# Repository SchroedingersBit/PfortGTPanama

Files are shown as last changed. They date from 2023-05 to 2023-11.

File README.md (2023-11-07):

# PfortGT World Final Panama 2023 🤖

## Introduction
This is the GitHub repository for the autonomous driving car of the **PfortGT Team** of the **Landesschule Pforta from Germany** for the **WRO Future Engineers World Final 2023 in Panama**.
In this repository we go into our planning - and building process for our car. We describe our problems and ideas we had along the way and explain our construction plans and programs.
## Overview
Our car is powered by an Arduino. It consists of a chassis which is equipped with individually 3D-printed mounts for the various sensors and the camera (see [components](/vehicle/components)). Power is supplied by a rechargeable battery (see [electronics](/vehicle/electronics)). The sensor equipment consists of three ultrasonic sensors, a gyro sensor and a Pixy Cam2 (see [sensors](/vehicle/sensors)). For the Open Challenge, an Arduino code processes the distance to the walls measured by the ultrasonic sensors and the tilt from the gyro sensor to make small steering adjustments to the car (see [Open Challenge](/programming/OpenChallenge)). In the Obstacle Challenge a camera script is also used (see [Obstacle Challenge](/programming/ObstacleChallenge)). This looks for red and green color signatures via the Pixy Cam and keeps them on the screen section (right or left) corresponding respectively.
## Structure
Our repository is divided into several subgroups in which each topic of focus is discussed.
### Development
In [development](/development) we describe some short overviews of our development path with the ideas we had during the process, the problems we faced and how we solved them.
### Programming
In [programming](/programming) we explain the important part of coding. We describe and explain our structure, the decision for C++ and the two focal points [Open Challenge](/programming/OpenChallenge) and [Obstacle Challenge](/programming/ObstacleChallenge), as well as our actual [Overall Program](programming/OverallRace).
### Vehicle
In [vehicle](/vehicle/) it is shown in detail how our car is built. The [components](/vehicle/components) of the car are shown, how they are assembled and which of them were bought or 3D-printed. In [electronics](/vehicle/electronics) we explain the wiring and discuss the regulation of the the power supply for the motors and sensors. Besides that we discuss the [motors](/vehicle/motors) the car is equipped with and the motivation behinde our decission. Furthermore, our used [sensors](/vehicle/sensors), their special feautures and their purposes are explained. Additionally, [3D printing](/vehicle/3Dprinting) lists our files and work for our printed parts.
### Pictures
In [pictures](/pictures) there are photos of the car from different angles as well as our team photo. 
### Performance videos
In [videos](/videos) Youtube links are deposited, which demonstrate the performance of our car in test tracks for the various tasks.
### Sources
In [sources](/sources) we document our sources of information. In addition, all our [purchases](/sources/purchases) and the installation paths with the associated setup instructions for the used software are stored.

<p align="center">
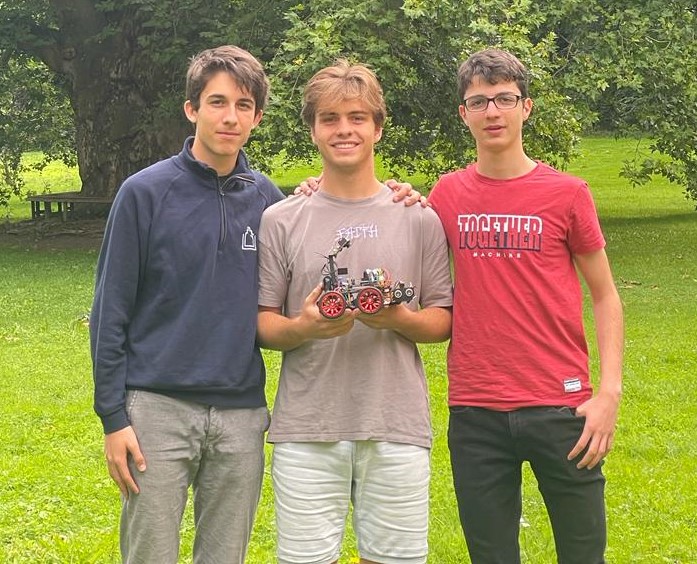
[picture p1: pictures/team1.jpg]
team photo

</p>

<p align="center">
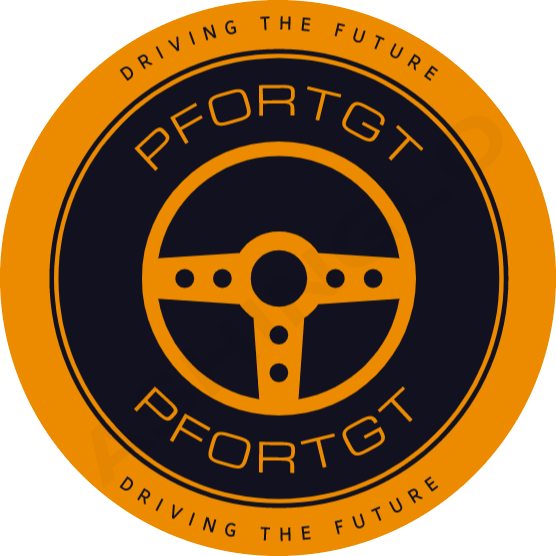
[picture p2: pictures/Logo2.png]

</p>

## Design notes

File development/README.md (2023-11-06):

# Development

First, the chassis was planned. It was important to keep the turning radius as small as possible and therefore the car short, while the steering, the motor and all other hardware components needed to fit on it. So the following first sketch (1:1) was made:

<p align="center">
  first chassis sketch
</p>

Now the type steering system had to be considered. The standard solution is an Ackermann steering mechanism, which works mechanically pretty well, but is hard to construct. In the following image, our first schematic sketch is seen, which helped us understanding the principles of the Ackermann steering mechanism.

<p align="center">
  Ackermann Steering sketch
</p>

The Rack and Pinion system is a more intuitive solution, which often does not work as good as the first one. Furthermore the lengths and dimensions of the steering knuckle and the tie-rod are important for preventing that the rear axle could break out. We developed a graphical calculation system using GeoGebra (which can be found in uploaded files/development) for determining fitting parameters. 

At the same time, we received the Funduino set, whose steering system we immediately adopted because it met our requirements. Instead we concentrated on minimizing the car dimensions and with that the turn radius and the chance of hitting obstacles.
We then printed more and more parts and were able to replace most of the parts with ours and also add additional components, such as the camera mount. Our first attempt of holding the camera was this construction:

<p align="center">
Bildschirmfoto 2023-11-06 um 11 56 43
</p>
Later, we realised, that a higher camera has higher chances to recognize the closer block of two obstacles and has generally a better overview. And just as predicted, the camera tower was created and performed better than the lower mount.
Still it had to be moved to the rear to ensure a better view. This helped to have a longer correction time and a better evaluation of the obstacle's position. 

This is our first attempt of placing the camera tower:

<p align="center">
  front placing camera tower
  
</p>

You can find a picture of the currently camera tower placement in [picture](https://github.com/SchroedingersBit/PfortGTPanama/blob/main/pictures).

(For understanding how each components were designed and built, have a look at [components](https://github.com/SchroedingersBit/PfortGTPanama/tree/main/vehicle/components).

A crucial change is also the exchange of the two gears, so that instead of a large to small transmission, there is a small to large transmission. Therefore, the car drives slower, but has a greater torque and does not stop at low speeds, thus overcoming greater static friction forces / rolling friction forces. This was needed since it often slowed down during steering to a minimum speed risking to stop and not being able to continue its drive. A greater torque and a lower speed also provides more time for calculating the new steering correction.
Another important step for increasing the time and power of computing was replacing the Arduino Uno with the Arduino Mega.

One of the last changes is the removal of the battery box. Even though it was a good variant to keep the battery away from hot pieces and still saved space on the cover plate, it sometimes touched the obstacles because of its protruding design. That's why we decided to not use the battery box, but strap the battery to the camera tower with cable ties, because it's a simple and functional option.

<p align="center">
  battery placement
  
</p>

For competition preparation we 3D-printed every component  and ordered our hardware electronic again, so we could substitute broken or loose pieces.

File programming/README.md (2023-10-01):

# Programming
All codes for the control of the car are stored here. All programs are written completely in C++, because we address all sensor data and motor steering via the Arduino. We use the official Arduino IDE. The program is composed of several classes, which are processed individually and can then be accessed as needed.

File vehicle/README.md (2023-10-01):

Here we describe which parts our robot is made of, which sensors and motors it has, how they are wired and which parts were printed with the 3D printer.

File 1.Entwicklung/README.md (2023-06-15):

# Entwicklung

Zuerst wurde das Chassis geplant. Wichtig dabei war, den Wenderadius möglichst klein und daher auch das Auto kurz zu halten. So entstand folgende erste Skizze:



Nun musste die Lenkung betrachtet werden. Die Standard Lösung ist eine Ackermann-Lenkung, welche bei falschen Maßen aber schnell dazu führt, dass die hintere Achse des Autos ausbricht. Hingegen ist die Rack and Pinion Lenkung schwerer zu bauen.
Im Endeffekt haben wir aus Zeitproblemen zunächst das fertige Chassis mit der gegebenen Elektronik und der fertigen Lenkung verändert. Später wurden noch viele weitere Veränderungen vorgenommen, bis wir auf dem Stand des jetzigen Modells sind (siehe Bau).

Eine entscheidende Veränderungen ist auch der Tausch der beiden Zahnräder, sodass anstatt einer groß- auf klein-Übertragung, eine klein auf groß-Übertragung vorliegt. Daher fährt das Auto zwar langsamer, hat aber ein größeres Drehmoment und bleibt bei niedrigen Geschwindigkeiten nicht stehen, überwindet also größere Haftreibungskräft/ Rollreibungskräfte.

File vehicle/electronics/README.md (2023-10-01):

# Electronics
## Cable color coding
**Voltage cable:**
* 🔴 red (5V driver, motors, gyro)
* 🟠 orange (motor IN)
* 🟡 yellow (ultrasonic sensors)

**Control cable:**
* 🟢 green: control cable for ENA, ENB and servo
* 🟡 yellow: Control cable gyro (SCL)
<br/>

* 🔵 blue: Gyro (SDA)
* 🟣 purple: ultrasonic sensor (Trig)
* 🔘 gray: ultrasonic senso (Echo)
* ⚫️ black: ground cable

## Driver
We use a L298N driver that can control two motors and has the ability to output 5V. As you can see in the picture below, we give the driver an input via the 12V input. Via the 5V output we supply our sensors as well as our IN1 or IN3 for motor activation and determination of the voltage direction. Via OUT1 and OUT2 we control our DC motor and via OUT3 and OUT4 we control our servo motor. Via a connection of ENA and ENB to our Arduino we regulate the voltage. The voltage of the servo motor is kept constant at 6.4V. We use the MG996R servo motor and a 3-9V DC motor from the Funduino set.

driver

## Arduino
We use the Arduino MEGA 2560 (Rev3) for increased computing power. In addition to the Arduino, we use an Arduino Uno Prototype Proto Shield V5 to have more pins available in a small space. We connected ground pins and voltage pins on the white board. Pins 2-7 are either trig or echo for the ultrasonic sensor. Pins 11 and 13 are ENA and ENB respectively and pin 9 is the control pin for the servo motor. The orange 3V cable supplies the gyro sensor, since it can withstand a maximum of 3.3V. The gyro sensor is therefore grounded directly via the Arduino.

Arduino

## Battery
We use a URGENEX 7.4V Li-ion battery for the power supply. The battery provides 7.4V with 2000mAh which is enough according to our calculations. Because the DC motor works very well with 7.4V and our current can be maximum 2A for a short time, which would allow us to work for an hour. The ground is connected to the switch, which is then connected to the ground pins.  

Batterie + Knopf

## Ultrasonic sensors
We use the HC-SR04 ultrasonic sensors, which are connected in front of the servomotors.

Servo + Ultraschall

## Overall picture
The entire representation was created using Fritzing, whereby additional components such as Driver, Gyro and Proto Shield V5 had to be implemented.
When building the circuit, we made sure to hide the cables as much as possible. This way our car looks nicer and the cables do not hinder the camera view.

Gesamtbild

## Charging the battery
We use the HTRC Lipo charger to charge our batteries. For this we have created our own charging program that charges each cell of the battery to a voltage of 3.7V with a current of 1A. The program can be accessed by pressing the Start button.

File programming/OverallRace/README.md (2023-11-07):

# Overall Race
The program contains a parameter that determines whether only the parts of the program that are important for the opening race must be used, since this does not require a camera script but only the ultrasonic sensors, or whether the camera data must also be used.

## RC_Control.ino
The program is started via the RC_Control.ino, which opens and manages all further classes.
```c++
//Include the required libraries and use the header files.
#include "variables.h"  // all the vars, actuators, and sensors are defined and initialized here.
#include "ControlRC.h"  // all functions for control, read sonsor and update variables are located here

//Create a serial connection, initialize the ports of the Arduino from the variable header and set th driving direction to forward.
void setup() {
  Serial.begin(9600);
  while (!Serial) delay(10);
  initializeHardware();
  drivingDC.setForward();
}

int secs = 6;
unsigned long Stoptime = 0;
int numRounds = 3;
// Instructions for the car
void loop() {

  updateControlData();
  drivingDC.drive(velocity); // velocity is a constant
  control_servo();
  
  //print(); // will be turned on for Debugging

  // Code to turn at the second round if he sees a redBlock
  if (redturn == 2 && turns == 8 && Sumcheck && redcheck) {
    tim = millis() + 1000;
    while (tim > millis()) {
      drivingDC.drive(velocity);
      steeringServo.drive(-1 * roll);
    }

    drivingDC.drive(0);
    drivingDC.setBackward();

    while (distances[1] + distances[2] < 150 || distances[0] < 150) {
      drivingDC.drive(velocity);
      steeringServo.drive(0);
    }

    tim = millis() + 1000;
    while (tim > millis()) {
      drivingDC.drive(velocity);
      steeringServo.drive(0);
    }

    drivingDC.drive(0);
    drivingDC.setForward();
    referenceAngle = referenceAngle + 90 * direction;
    theoreticalAngle = theoreticalAngle + 90 * direction;

    while (distances[1] + distances[2] > 150 || distances[0] > 150) {
      updateControlData();
      drivingDC.drive(velocity);
      control_servo();
    }

    direction = direction * (-1);
    redcheck = false;
  }

  // Termination condition after 3 laps have been run
  if (turns == 4 * numRounds) { // 12 turns achieved
    Stoptime = millis() + secs * 1000; // 
    while (distances[0] > 120 || !Sumcheck || Stoptime > millis()) {  // drive for at least Stoptime and until frontDistance is less than 120 and SumDistance is less than 100
      updateControlData();
      drivingDC.drive(velocity);
      control_servo();
    } // turn everything off
    while (1) {
      control_servo();
      drivingDC.drive(0);
      delay(100);
    }
}

// different sensor data in the serial monitor for bugfixing and understanding what the robot is doing
void print() {
  float k = (distances[0] - (67578.1 / (cam.get_Blocksize() + 514.89) - 13.4431) - 80) * (0.5 * direction * (abs(cam.get_color() - 1) - min(1, 2 - cam.get_color())) + max(0.5, 1 - 0.5 * cam.get_color()));
  Serial.print("referenceAngle ");
  Serial.print(referenceAngle);
  Serial.print("       targetAngle ");
  Serial.print(controlDataArr[0]);
  Serial.print("       roll ");
  Serial.print(roll);
  Serial.print("       rightShift ");
  Serial.print(rightShift);
  Serial.print("       camShift ");
  Serial.print(camShift);
  Serial.print("       wallShift ");
  Serial.print(wallShift);
  Serial.print("       frontdistance ");
  Serial.print(distances[0]);
  Serial.print("       rightdistance ");
  Serial.print(distances[1]);
  Serial.print("       leftdistance ");
  Serial.print(distances[2]);
  Serial.print("       sumdistance ");
  Serial.print(distances[2] + distances[1]);
  Serial.print("       sumcheck ");
  Serial.print(Sumcheck);
  Serial.print("       size ");
  Serial.print(cam.get_Blocksize());
  Serial.print("       Blockdistance ");
  Serial.print(k);
  Serial.print("       function ");
  Serial.print(k < 0 && k > -35 ? 0 : 1);
  Serial.print("        x_pos  ");
  Serial.print(cam.get_x_pos());
  Serial.print("        frameWidth  ");
  Serial.print(cam.get_frameWidth());
  Serial.print("        correction ");
  Serial.print(1 - 1 / cam.get_frameWidth() * abs(cam.get_x_pos()));
  Serial.print("       color ");
  Serial.println(cam.get_color());
}

```

## ControlRC.h
This header file contains all the logic for the car and ensures that the measured values are updated and calculated at the right time. This logic then passes on the new adjustments to the steering.

```c++
#ifndef Control_h
#define Control_h

//Include the required libraries.
#import <math.h>
#include "variables.h"

// returns the Sign of the number
int getSign(int number) {  // returns 1 when its positive and returns -1 when its negative
  return (number >= 0) ? 1 : -1;
}

// Verification that roll ic close to reference angle
void checkSafeAngle() {
  if (abs(referenceAngle - roll) <= 12)
    safeAngle = true;
  else
    safeAngle = false;
}

// check if he is near the wall when he sees a block and calculate a relative wallShift depending on the color seen and wallDistance
void checkSafeDistance() {                                                                            if (distances[1] * max(0, color - 1) + distances[2] * (1 - abs(color - 1)) - wallDistance * min(1, color) < 0) {
    wallcheck = 0;
    wallShift = (wallDistance - distances[1]) * (color - 1) + (distances[2] - wallDistance) * (2 - color);
  } else {
    wallcheck = 1;
    wallShift = 0;
  }
}

// checl if he is in a straight path
void checkSafeSum() { 
  if (distances[2] + distances[1] < 100 && safeAngle && distances[0] < 200) {
    Sumcheck = true;
  }
}

// Examination under various conditions as to whether a curve is recognized
void checkCurve() {
  if (distances[2] + distances[1] >= 140 && Sumcheck) {
    if (distances[0] < 100) {
      if (safeAngle) {
        if (Blockcheck || (!Blockcheck && abs(x_pos) - 45 > 0)) {
          if (abs(distances[2] - distances[1]) > 20) {
            sign = (1 - abs(direction)) * getSign(distances[1] - distances[2]) + direction;
            referenceAngle = referenceAngle + sign * 90;
            theoreticalAngle = theoreticalAngle + sign * 90;
            direction = sign;
            Sumcheck = false;
            turns += 1; 
          }
        }
      }
    }
  }
}

// when the robot isnt placed well he corrects that
void updateReference() {
  if (safeAngle)
    if (abs(rightShift) - abs(lastShift) >= 0) 
      referenceAngle = roll;
  sign = getSign(referenceAngle - theoreticalAngle);                                                
  referenceAngle = (abs(referenceAngle - theoreticalAngle) > 2 ? theoreticalAngle + sign * 2 : referenceAngle); 
}

// getting new sensor data
void updateSensorData() {
  manager.readDistances(distances);
  roll = orientation.getTotalRoll();
}

// getting the data from the camera
void updateCameraData() {
  cam.BlockData(Sumcheck);
  color = cam.get_color();
  x_pos = cam.get_x_pos();
  frameWidth = cam.get_frameWidth();
  Blockcheck = cam.get_Blockcheck();
  area = cam.get_Blocksize();
}

// Performs previous functions
void updateChecks() {
  checkSafeSum();
  checkSafeAngle();
  checkSafeDistance();
  checkCurve();
}

// it is started by RC_Control.ino and starts other functions, calculates the different angles and adjustments
void updateControlData() {
  updateSensorData();
  updateCameraData();
  updateChecks();

  int frontDistance = distances[0];
  int rightDistance = distances[1];
  int leftDistance = distances[2];

  // saving the color of the last Block till the eights turn!!
  if (turns < 8 && !Blockcheck)
    redturn = color;
  else if (turns == 8 && !Blockcheck && area > 300 && !Sumcheck)
    redturn = color;

  // the following code calculates the targe_car_angle from the sensor Data

  // calculating rightShift
  rightShift = (leftDistance - rightDistance) * max(0, 1 - color * Run);

  // calculating camShift 
  float cam_Steering = ((1.4 - 0.4) / (2 * frameWidth) * (2 * color - 3) * x_pos + (1.4 + 0.4) / 2) * (abs(referenceAngle - roll) > 20 && (frontDistance < 10 || leftDistance * (2 - color) + rightDistance * (color - 1) < 20) ? 0 : 1) + 2.5 * abs(Sumcheck - 1);
  camShift = (frameWidth * (3 * min(1, color) - 2 * color) - x_pos) * cam_Steering * wallcheck * min(1, Sumcheck + (direction * x_pos * (color * (color + direction) == 2 ? 0 : 1) >= -80 && area >= 200 ? 1 : 0)) * Run + wallShift;

  // calculating the target_car_angle
  const float FACTOR_Steering = 1.25f;
  float target_car_angle = -1 * FACTOR_Steering * (rightShift + camShift) + referenceAngle;

  updateReference();

  //looking if the target_car_angel is in the Bounds

  // lowerBound helps the robot to drive in the middle
  float lowerBound = (Sumcheck ? min(30, max(0, 0.30 * frontDistance - 30)) : 0);
  // upperBound makes sure that the car isn't far away from the referenceAngle
  int upperBound = 25;
  //Blockbound lets the car turn a lot if a Block is detected
  float BlockDistance = (frontDistance - (67578.1 / (area + 514.89) - 13.4431) - 80) * (0.5 * direction * (abs(color - 1) - min(1, 2 - color)) + max(0.5, 1 - 0.5 * color));
  float Blockbound = (130 + 55 * abs(Sumcheck - 1)) * (BlockDistance < 0 && BlockDistance > -35 || area < 100 ? 0 : 1) + abs(1.25 * wallShift + 25) * abs(wallcheck - 1);

  // Here the Bounds are checked and if necessary, the target_car_angle will be updated
  sign = getSign(target_car_angle - referenceAngle);
  if (!Blockcheck * Run)
    target_car_angle = (abs(target_car_angle - referenceAngle) >= Blockbound ? referenceAngle + sign * Blockbound : target_car_angle);
  else if (abs(roll - referenceAngle) > upperBound)
    target_car_angle = referenceAngle;
  else
    target_car_angle = (abs(target_car_angle - referenceAngle) >= lowerBound ? referenceAngle + sign * lowerBound : target_car_angle);

  controlDataArr[0] = target_car_angle;
  lastShift = rightShift; 
}

// Forward the calculated data to the servo, thus adjusts the steering.
void control_servo() {
  float target_car_angle = controlDataArr[0];
  float err = target_car_angle - roll;
  steeringServo.drive(err * 0.1);
}
#endif
```

## variables.h
Here all important variables as well as pins for the Arduino are stored, which are needed for the program.
```c++
#ifndef variables_H
#define variables_H

// include the required libarries
#include <Arduino.h>
#include "CarOrientation.h"
#include "UltrasonicManager.h"
#include "MyServo.h"
#include "MyDC.h"
#include "camera.h"

// declaring the pins

// declaring the pins for the ultrasonic sensors
const uint8_t frontTrigPin = 2;
const uint8_t frontEchoPin = 3;
const uint8_t rightTrigPin = 4;
const uint8_t rightEchoPin = 5;
const uint8_t leftTrigPin = 6;
const uint8_t leftEchoPin = 7;
UltrasonicManager manager(frontTrigPin, frontEchoPin, rightTrigPin, rightEchoPin, leftTrigPin, leftEchoPin);

// declaring the pin for the Servo motor
byte servoPin = 9;
MyServo steeringServo(servoPin, servo_PWMpin);

// declaring the pin for the DC-motor
byte DC_PWMpin = 11;
MyDC drivingDC(DC_PWMpin);

// declaring the gyro-sensor
CarOrientation orientation;

// declaring the camera
camera cam;

//defining global variables
float controlDataArr[] = { 0, 0 };  //[desired Car Angle, Speed]
float distances[] = { 0, 0, 0 };
float roll;
float referenceAngle = 0;
float theoreticalAngle = 0;
int wallDistance = 20;
int wallcheck;
float wallShift;
float rightShift;
float camShift;
int turns = 0;
bool safeAngle;
bool Sumcheck = true;
float lastShift = 10000000;
int velocity = 40;
int direction = 0;
int sign;
int color;
int x_pos;
int frameWidth;
int Blockcheck;
int area;
int redturn;
bool redcheck = true;
int Run = 1;  //0 for open Challenge and 1 for obstacle Challenge

// initialize the sensors and motors
void initializeHardware() {
  steeringServo.init();
  drivingDC.init();
  cam.init();
  if (!orientation.init()) {
    Serial.println("Failed to initialize CarOrientation");
    while (1) {
      delay(10);
    }
  }
}
#endif
```

## UltrasonicManager.h
Here, the ultrasonic sensor data is read out and then the median is calculated for five values each.
```c++
#ifndef UltraSonic_h
#define UltraSonic_h

// include the required libarries
#include <NewPing.h>
#include <RunningMedian.h>

#define MAX_DISTANCE 400  // maximal distance in cm
#define BUFFER_SIZE 7    // Number of measurements saved for the median calculation

// connection between Pins and Arduino, median for minimizing measurement errors 
class UltrasonicManager {
private:
  NewPing frontSensor;  // Front Sensor
  NewPing rightSensor;  // Right Sensor
  NewPing leftSensor;   // Left  Sensor
  unsigned int frontDistance;
  unsigned int rightDistance;
  unsigned int leftDistance;
  RunningMedian median_front;
  RunningMedian median_right;
  RunningMedian median_left;

public:
  UltrasonicManager(uint8_t frontTrigPin, uint8_t frontEchoPin, uint8_t rightTrigPin, uint8_t rightEchoPin, uint8_t leftTrigPin, uint8_t leftEchoPin)
    : frontSensor(frontTrigPin, frontEchoPin, MAX_DISTANCE),
      rightSensor(rightTrigPin, rightEchoPin, MAX_DISTANCE),
      leftSensor(leftTrigPin, leftEchoPin, MAX_DISTANCE),
      median_front(BUFFER_SIZE),
      median_right(BUFFER_SIZE),
      median_left(BUFFER_SIZE) {}

  // get the Data from the Ultrasonic sensors
  void readDistances(float distances[3]) {
    int frontMess = frontSensor.ping_cm();
    int rightMess = rightSensor.ping_cm();
    int leftMess = leftSensor.ping_cm();

    // sort our mismeasurements
    if (frontMess != 0)
      median_front.add(frontMess);
    if (rightMess != 0)
      median_right.add(rightMess);
    if (leftMess != 0)
      median_left.add(leftMess);

    // take the median
    frontDistance = median_front.getMedian();
    rightDistance = median_right.getMedian();
    leftDistance = median_left.getMedian();

    // save the data in an array
    distances[0] = frontDistance;
    distances[1] = rightDistance;
    distances[2] = leftDistance;
  }
};
#endif

```

## MyServo.h
Here the servo is addressed and the steering instructions from ControlRC.h are converted into the appropriate servo voltages.
```c++

#ifndef MyServo_h
#define MyServo_h

// include the required libarries
#include <Arduino.h>
#include <Servo.h>

class MyServo {
private:
  // define the Control Pin
  byte pin;
  byte limitR = 133;   // Right limit for servo angle
  byte limitL = 20;    // Left limit for servo angle
  byte straightAngle = 90;  // Default angle for a straight position
  Servo steeringServo;

public:
  MyServo() {}    // Default constructor (empty)

  MyServo(byte pin) {
    this->pin = pin;
  }

  // Initialize the servo and set its initial position
  void init() {
    steeringServo.attach(pin);
    pinMode(pin, OUTPUT);
    reset();
  }

  // Reset the servo to the straight position
  void reset() {
    steeringServo.write(straightAngle);
  }

  // Control the servo angle based on the provided value
  // value = 0 => straightAngle; value = 1 => limitR; value = -1 => limitL
  double drive(float value) {
    value = min(1, max(-1, value));  // Ensure value is between -1 and 1
    int sgn = (value == 0 ? 0 : 0.5 * value / abs(value) - 0.5);
    value = (limitR * (sgn + 1) + limitL * sgn - straightAngle * 2 * (sgn + 0.5)) * value + straightAngle;
    // Calculate the angle based on the provided value
    steeringServo.write(value);  // Set the servo angle
    return value;
  }
};
#endif

```

## MyDC.h
Here the required DC-Moter voltage is calculated, which is necessary to guarantee the required speed from the other programs.
```c++
#ifndef MyDC_h
#define MyDC_h

#include <Arduino.h>

// Define a class named MyDC
class MyDC {
private:
  byte speedPin;  // Pin to control motor speed
  byte pinIN1;    // Motor input 1
  byte pinIN2;    // Motor input 2

public:
  // Default constructor (empty)
  MyDC() {}  

  // Parameterized constructor to initialize the motor pins
  MyDC(byte speedPin, byte pinIN1, byte pinIN2) {
    this->speedPin = speedPin;
    this->pinIN1 = pinIN1;
    this->pinIN2 = pinIN2;
  }
  // Initialize the motor pins as outputs
  void init() {
    pinMode(speedPin, OUTPUT);
    pinMode(pinIN1, OUTPUT);
    pinMode(pinIN2, OUTPUT);
  }

  // Drive the motor at a specified speed (0-100)
  void drive(float speed) {
    speed = (speed > 100) ? 100 : speed;  // Ensure speed is <= 100
    speed = (speed > 0) ? max(40, speed) : speed;  // Ensure a minimum speed of 40
    speed = map(speed, 0, 100, 0, 255);  // Map speed to the PWM range
    analogWrite(speedPin, speed);  // Set the motor speed
  }

  // Set the motor to move forward
  void setForward() {
    digitalWrite(pinIN1, LOW);
    digitalWrite(pinIN2, HIGH);
  }
  // Set the motor to move backward
  void setBackward() {
    digitalWrite(pinIN1, HIGH);
    digitalWrite(pinIN2, LOW);
  }
};
#endif

```

## CarOrientation.h
Here, the gyro sensor data is handled to determine the vehicle orientation and the angle of rotation traveled.
```c++
//include the required libarries
#include <Wire.h>
#include <Adafruit_BNO08x.h>

//Detection and calculation of vehicle alignment using data from the BNO08x sensor (gyroscope)
class CarOrientation {
private:
  Adafruit_BNO08x bno;
  sh2_SensorValue_t sensorValue;
  float initialAngle[3] = { 0.0, 0.0, 0.0 };
  float lastAngle[3] = { 0.0, 0.0, 0.0 };
  float totalRotation[3] = { 0.0, 0.0, 0.0 };
  bool initialAngleSet = false;

public:
  CarOrientation() {}
  //Initializes the BNO08x sensor and sets the corresponding reports.
  bool init() {
    if (!bno.begin_I2C()) {
      Serial.println("Failed to find BNO08x chip");
      return false;
    }
    setReports();
    delay(100);
    return true;
  }
  // Activates the required reports for the BNO08x sensor
  void setReports() {
    if (!bno.enableReport(SH2_GAME_ROTATION_VECTOR)) {
      Serial.println("Could not enable game vector");
    }
  }

  float quaternionToRoll(float qw, float qx, float qy, float qz) {
    float roll = atan2(2.0f * (qw * qz + qx * qy), qw * qw + qx * qx - qy * qy - qz * qz);
    return roll * (180.0 / M_PI);
  }
  //Updates the sensor values and calculates the vehicle alignment based on the quaternions
  void update() {
    if (bno.wasReset()) {
      setReports();
    }

    if (!bno.getSensorEvent(&sensorValue)) {
      return;
    }

    if (sensorValue.sensorId == SH2_GAME_ROTATION_VECTOR) {
      float qw = sensorValue.un.gameRotationVector.real;
      float qx = sensorValue.un.gameRotationVector.i;
      float qy = sensorValue.un.gameRotationVector.j;
      float qz = sensorValue.un.gameRotationVector.k;
      float roll = quaternionToRoll(qw, qx, qy, qz);

      if (!initialAngleSet) {
        lastAngle[2] = roll;
        initialAngle[2] = roll;
        initialAngleSet = true;
      } else {
        float deltaRoll = roll - lastAngle[2];

        if (deltaRoll > 180.0) {
          deltaRoll -= 360.0;
        } else if (deltaRoll < -180.0) {
          deltaRoll += 360.0;
        }

        totalRotation[2] += deltaRoll;
        lastAngle[2] = roll;
      }
    }
  }

  // Returns the relative roll angle change of the vehicle.
  // The relative roll angle is the roll angle compared to the initial position of the vehicle.
  // The value is negated to provide the roll angle in the correct orientation.
  float getRelativeRoll() {
    update();
    return (quaternionToRoll(sensorValue.un.gameRotationVector.real, sensorValue.un.gameRotationVector.i, sensorValue.un.gameRotationVector.j, sensorValue.un.gameRotationVector.k) - initialAngle[2]) * -1;
  }

  // Returns the total roll angle of the vehicle.
  // The total roll angle is the sum of all roll angle changes since the initial position of the vehicle.
  // The value is negated to provide the roll angle in the correct orientation.
  float getTotalRoll() {
    update();
    return totalRotation[2] * -1;
  }

  //Resets the initial angle and the status for the vehicle alignment
  void reset() {
    initialAngleSet = false;
  }
};

```

## camera.h
In camera the properties of the largest detected color block, such as color value height and width are output.
```c++
//include the required libarry
#include <Pixy2.h>

//search for red or green Block: green = 1 and red = 2
class camera {
private:
// declare the variables
  Pixy2 pixy;
  uint16_t Width;
  uint16_t Height;
  int8_t Blocks;
  uint16_t signature;
  int m_x;
  uint16_t m_y;
  unsigned long time;
  int last_signature = 0;
  int new_signature;
  bool Block_test;
  bool timer = true;
  int size;

public:
  camera() {}

  void init() {
    pixy.init();
    Width = pixy.frameWidth / 2 ;  // Width = 158
    Height = pixy.frameHeight; // Height = 208
  }

  // looking for a block
  void BlockData(bool Adder) {
    Block_test = true * timer;
    Blocks = pixy.ccc.getBlocks();  // getting the data from the camera
    if (Blocks && timer) {  // if any Block it detected and no change of Blocks were detected
      for (int i = 0; i < Blocks; i++) { // look through the blocks from the biggest to the smallest
        m_y = pixy.ccc.blocks[i].m_y;
        if (m_y >= Height * 0.2 && m_y <= Height * 0.85) { // the Block shouldn't lie high or low in the frame
          // get the Block Data
          new_signature = pixy.ccc.blocks[i].m_signature;
          m_x = pixy.ccc.blocks[i].m_x - Width;
          Block_test = false;
          size = pixy.ccc.blocks[i].m_width * pixy.ccc.blocks[i].m_height;
          break; // stop if a block was detected
        }
      }
  }
  // to ensure the car doesn't hit the block immediatly when he stops seeing the Block we built a timer, to save the old data of the Block untill timer becomes true
  if (Block_test && timer) { // reset the variables
      new_signature = 0;
      m_x = 0;
      size = 0;
    } // start timer when he switches from block seen to no block seen or their was a change of color
    if (last_signature != 0 && (Block_test || (!Block_test && last_signature != new_signature))) {
      signature = last_signature;
      timer = false;
      time = millis() + 100UL + 100UL * !Adder;
    } else if (timer) {
      signature = new_signature;
    } // check whether the time has elapsed
    if (time < millis() && !timer)
      timer = true;

    last_signature = new_signature;

  int get_x_pos() {
    return m_x;
  }
  int get_color() {
    return signature;
  }
  int get_frameWidth() {
    return Width;
  }
  int get_Blockcheck() {
    return Block_test;
  }
  int get_Blocksize() {
    return size;
  }
};

```

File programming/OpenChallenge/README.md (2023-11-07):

# Open Challenge
In the opening race, the car incorporates ultrasonic and gyroscope sensor data in order to be able to drive in the center between the set-up boundaries. If it is not in the center, e.g. because of a curve or inaccuracies, a new angle - target angle from the different distances to the walls - rightshift is calculated, which should be aimed at. This angle is then slowly corrected to prevent a jerky movement and must not exceed a maximum size, which is defined by the gyro sensor. The gyro sensor also counts the covered curves to stop after three rounds. The ultrasonic sensor value results from the median of 5 measurements and is updated all the time.
## Flowchart for the ultrasonic sensors
```mermaid
flowchart TB;
USS-Code --> D(distance < 400) --> Median;
subgraph Median
N(new measurement) -->|update oldest measurement| M(5 measurements)-->ME[calculate median] --> N;
end
Median --> Rightshift;

subgraph Rightshift
LR(difference left right USS) --> |formula calculations| W[angle for steering];
end
Rightshift --> Steering;

subgraph Steering
Calculations --> S[servo angle to set]
end
Steering --> Z(car adjusts steering)
```

## Flowchart for curve logic
```mermaid
flowchart TB;

curve --> | left + right USS >= 140| D;

subgraph  CheckSafeSum
D(left + right USS <100) --> |car tilt <= 12| Front2[Front USS];
Front2 --> |Measured value < 200| Straight(car was in a straight section);
end

Straight --> F[Front USS];
F--> |Measured value < 100| Gyrosensor;
Gyrosensor --> |car tilt <= 12 | B(no block in front of camera);
B --> |absolut of left - right USS > 20| C[curve check]
C --> |rightshift < 0| R(right curve);
R --> |reference angle + 90 |K[finish curve, store curve type];
C --> |rightshift > 0| L(left curve);
L --> |reference angle - 90 |K;

```

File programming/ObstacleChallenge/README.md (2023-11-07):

# Obstacle Challenge

In the obstacle race, we use the property of the Pixy Cam to detect different color blocks, green and red for the competition. As long as the PixyCam does not register any color blocks, the variable color=0 and the program continues to run normally, without any disctractions from the camera. As soon as a color block is detected, color is set to 1 for green and 2 for red. The influence of the ultrasonic sensors on the steering is now reduced in order to concentrate on the steering inputs from the camera. If the car exceeds a threshold value for the distance to the walls, a steering adjustment is made to center it again.  A new steering angle - camera shift - is calculated using the distance between the block and the edge of the camera frame.  The further to the left a red block is in the frame, for example, the smaller the steering adjustment. A short timer has been built in to prevent the car from shifting the block when driving around it due to the next steering adjustments, as the camera can no longer see it.

## Overview
```mermaid
flowchart TB;
classDef redFill fill:#ff6666,stroke:#333,stroke-width:2px;
classDef greenFill fill:#66ff66,stroke:#333,stroke-width:2px;
Obstacle --> P{PixyCam detects color} -->|reduce USS influences| R{2 - red right} & G{1 - green left};
R --> |measueres distance block to left-corner in camera frame| S{calculate steering angle};
G --> |measueres distance block to right-corner in camera frame| S;
S --> |no more color detected or small distance to walls| B{center position to walls};
class R redFill;
class G greenFill;
```

## Cam_Steering
The steering of the vehicle should decrease when the block is further and further to the left or right of the camera, depending on the color. To ensure this, we let the cam_steering_factor decrease linearly. And then we let the steering_factor become zero when it is close to the wall. It is important that we let the factor increase when the car is in a curve so that the car can avoid the obstacle. The Cam_steering factor is then multiplied to the cam_Shift variable.
```mermaid
flowchart TB;
classDef redFill fill:#ff6666,stroke:#333,stroke-width:2px;
classDef greenFill fill:#66ff66,stroke:#333,stroke-width:2px;
Obstacle --> P[PixyCam detects color]
P --> |red| R(increase from left to right)
P --> |green| G(decrease from right to left)
P --> |near wall| H(set cam_steering to zero)
H --> J{first cam_steering factor}
G --> J{first cam_steering factor}
R --> J{first cam_steering factor}
Curve --> Q{second cam_steering factor}
J --> |Sum| L{cam_steering factor}
Q --> |Sum| L{cam_steering factor}
```
And here you can see the linear functions which rose from this function $$f(color, x_{pos}) = \frac{(1.4 - 0.4)}{(2 * frameWidth)} * (2 * color - 3) * x_{pos} + \frac{(1.4 + 0.4)}{2}$$.
<table align="center">
  <tr>
    <td align="center">
      green_cam_steering
      <p>color = 1</p>
    </td>
    <td align="center">
      Red_cam_steering
      <p>color = 2 </p>
    </td>
  </tr>
</table>

## Cam_Shift
In our code we calculate the position of the Block to its corresponding edge with this formula $$frameWidth * (3 * \min(1, color) - 2 * color) - x_{pos}$$. Furthermore this function is then multiplied by cam_Steering to strongen or weaken the effect of the cam_Shift. There is still more parameters that are multiplied with cam_Shift to ensure a safe drive.
```mermaid
flowchart TB;
classDef redFill fill:#ff6666,stroke:#333,stroke-width:2px;
classDef greenFill fill:#66ff66,stroke:#333,stroke-width:2px;
Obstacle --> P[PixyCam detects color]
P --> |get x_pos| L[calculate the relative position to the edge and multiply by cam_Steering]
L --> |near wall| U[cam_Shift = 0]
L --> |away from wall| V{in Curve}
V --> |green, turn left and x_pos > 30| W[Cam_Shift = 0]
V --> |red, turn right and x_pos < -30| M[Cam_Shift = 0]
V --> |else| Y{return cam_Shift}
```

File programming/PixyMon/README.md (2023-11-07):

## Signature
We use PixyMon with the help of Color Connected Components (CCC) to train our Pixy2 to see the color of an object. The color code for an object of the desired color is stored by holding it in front of the camera and selecting the object. After that, further adjustments are made to make the recognition as precise as possible. The PixyCam can detect an enormously high number of objects simultaneously. However, we only need four objects with a total of two different color codes at a time. The PixyCam then automatically sorts the object with the searched color code, which takes up the most frames on the screen, as the first block.
It is important to save the green Block in the first signature and the red Block in the second signature, because we 1 for green and 2 for red. 
<p align="center">
Signature label
</p>

## communication
Since we want to communicate with the arduino, it is important to set the right Data out port and to make the baudrate high for faster communication
<p align="center">
Interface
</p>

## Built-in functions
The camera itself has a number of corrections that should be activated. Auto exposure correction helps with an overexposed room. If you activate this function, the camera can also see in overexposed rooms.
In addition, flicker avoidance eliminates the flickering of the light source. The auto white balance can be switched on temporarily so that the camera gets used to the new light temperature.
<p align="center">
  
  
</p>

## Tuning
There are many ways to tune the block detection. After some experiments, we came up with these values that need to be improved in the competition
<p align="center">
Expert
Signature label
</p>

## Result
With the right settings and values, we are able to recognize up to 4 blocks very clearly at the same time.
<p align="center">

</p>
For more information on which setting has which effect and how to reduce false-positive and positive-false readings, please visit the official Pixyxcam website, where there is clear documentation on how to use PixyMon and how to set up Pixycam. 
The links can be found in

[sources](https://github.com/SchroedingersBit/PfortGTPanama/tree/main/sources/programming).

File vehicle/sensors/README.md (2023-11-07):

# Sensors
Here the sensors are described and their properties explained.
## PixyCam
The PixyCam 2 was chosen for the camera. This is a popular choice for robotics projects involving autonomous driving cars for several reasons. First, it provides a reliable and accurate image processing function specifically designed for object detection and tracking. This enables the autonomous vehicle to acquire visual information in real time and make decisions based on the detected objects.
Another advantage of the PixyCam 2 is its ease of use. It has a simple interface and a well-documented API that facilitates integration with different platforms and programming languages. This is very convenient for us, since the library for Arduino is very easy to set up and there are many sources available. In addition, the PixyCam 2 is characterized by its compact size and low power consumption, which makes it ideal for use in autonomous vehicles, where space and energy efficiency are important factors.

The PixyCam2 is connected to the Arduino via a ICSP SPI cable with three ports and communicates through the ICSP connector. To train the PixyCam 2 to the color codes of certain objects, the PixyMon software is used.

<p align="center">
  PixyCam
</p>

## Ultrasonic sensors
The use of the HC-SR04 ultrasonic sensors allows us, especially for the opening race, detect distances to walls in the vicinity of the vehicle. They emit ultrasonic waves and measure the distance through the time it takes for the reflected signal to return: $d=\lambda \nu *t$.  This is crucial to avoid collisions with walls and drive the curves safely. Another advantage is their versatility. They can be mounted in different directions and angels to cover a wide field of view. This allows us to guarantee comprehensive and reliable environmental awareness for the car. Ultrasonic sensors operate independently of lighting conditions such as glare or reflections, which can occur with other sensors such as cameras. However, we had to deal with a big problem regarding reflections of the ultrasonic waves from slanted walls. Only a slightly slanted wall which often occurs in the race areas, could affect the distance to it a lot. We tried to fix this as much as possible in our program through error tolerances and sensor data conditions. Nevertheless, we can not trust the sensors enough to rely only on their data. We therefore installed a gyro sensor, which operates more accurate. The ultrasonic sensors then only work in the event of deviations that are no greater than 12 degrees or if threshold values to the walls are exceeded and therefore largely serve as a hedge.

<p align="center">
  US sensor
   US sensor
</p>

## Gyroscope
To stop the car after three laps and know the spatial orientation, the Adafruit 9-DOF Orientation IMU Fusion Breakout - BNO085 (BNO080) gyroscope was installed. It measures the rotated angles during turns and brings the motor to a stop after 1080° of rotation or 12 curves. To prevent stopping earlier due to rotations while steering, a specific limit must be exceeded to count as a curve. As we described earlier, the gyroscope is important for the steering, as it ensures a straight driving. If there is no block detected or the front distance to a wall is not too small, the steering angle is calculated through the gyroscope data with the goal to do not leave a specific interval of the car orientation.
The BNO085 uses a combination of accelerometer, gyroscope, and magnetometer data to calculate its orientation, and it does so using a sensor fusion algorithm that is more accurate than any of the individual sensors on its own. The high precision of the sensor was the moving reason for choosing it.

<p align="center">
  Gyroscope
</p>

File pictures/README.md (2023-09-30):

# Vehicle and team photos
Here you can find the photos of the complete robot from different views and our team photo. In [photosAlt.md](photosAlt.md) you can see older photos of our robot.
## Front view

<p align="center">
  Front1
</p>

## Back view

<p align="center">
  Back1
</p>

## Top view

<p align="center">
  Top1
</p>

## Bottom view

<p align="center">
  Bottom1
</p>

## Side view

<p align="center">
  Side1
  Side2
</p>

## Team photo

<p align="center">
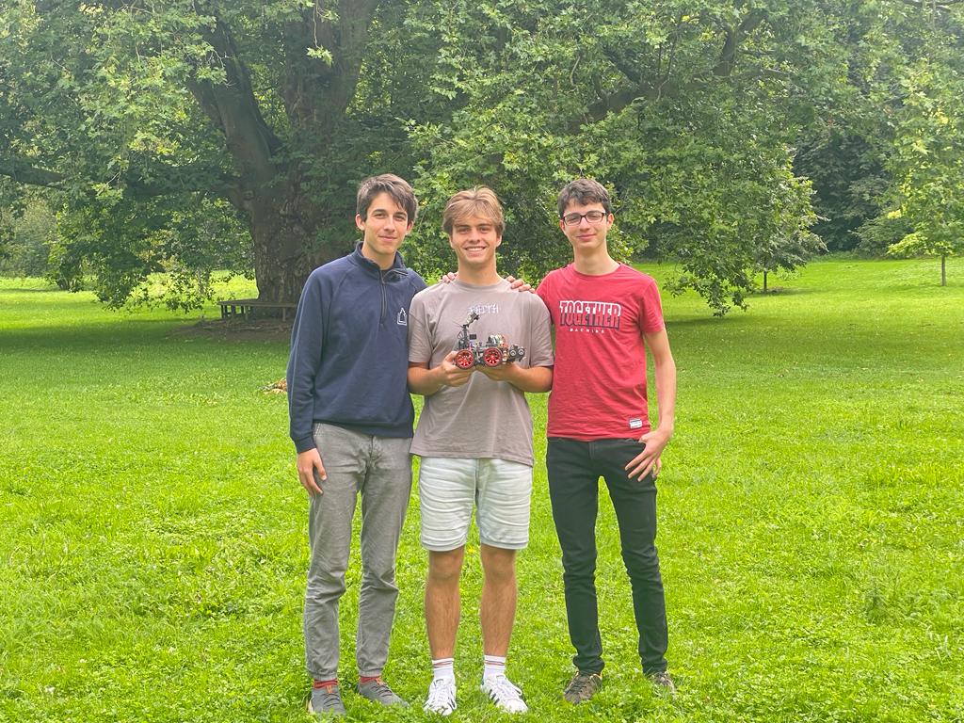
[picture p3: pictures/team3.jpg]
Team
  
</p>

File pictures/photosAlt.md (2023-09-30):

# Vehicle pictures for the first competition round in Chemnitz Germany
Here are the photos of the old robot from different views:
## Front view

<p align="center">
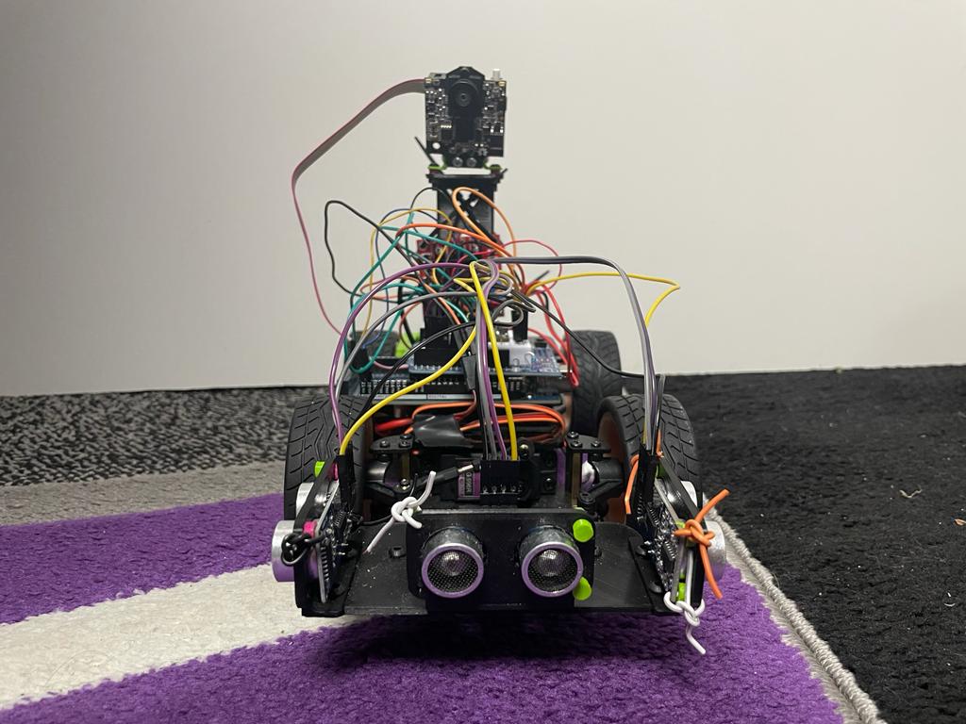
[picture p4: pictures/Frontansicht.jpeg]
Front
  
</p>

## Back view

<p align="center">
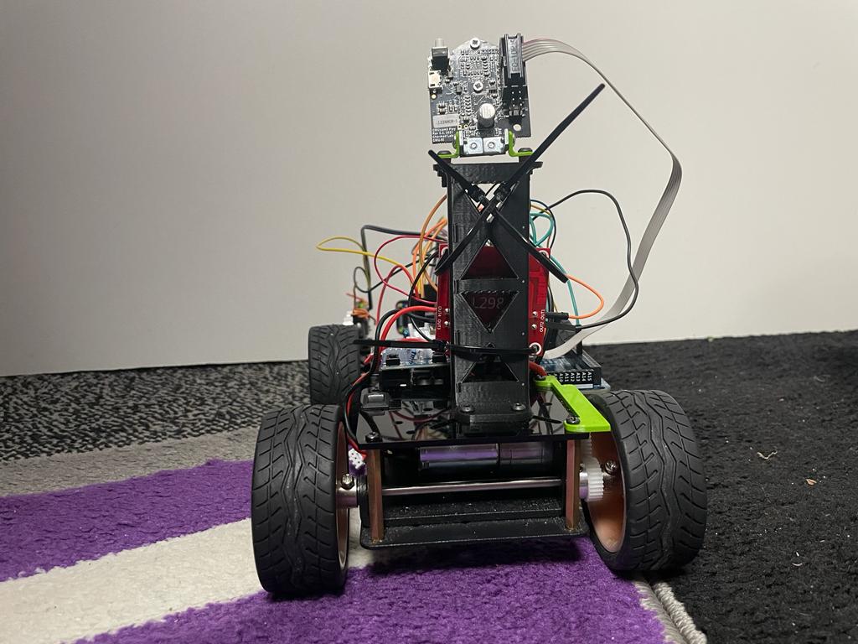
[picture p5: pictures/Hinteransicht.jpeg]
Hinten
  
</p>

## Top view

<p align="center">
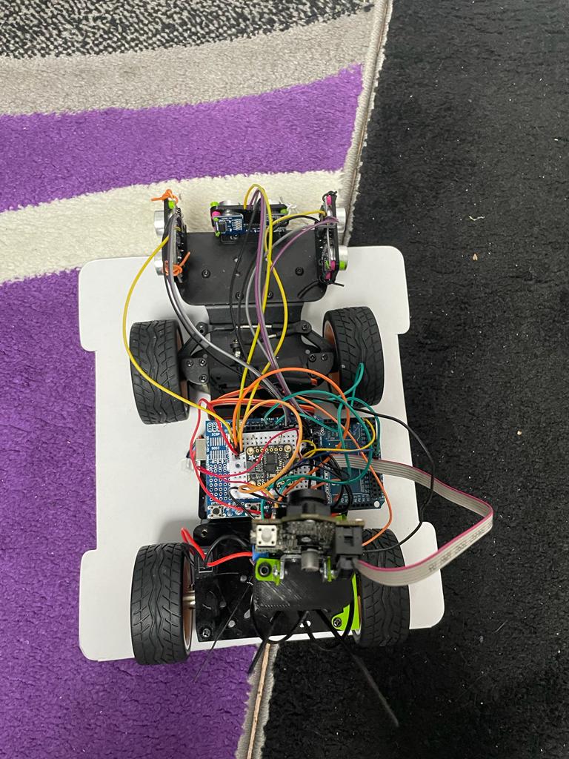
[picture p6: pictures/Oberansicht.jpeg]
  
</p>

## Side view

<p align="center">
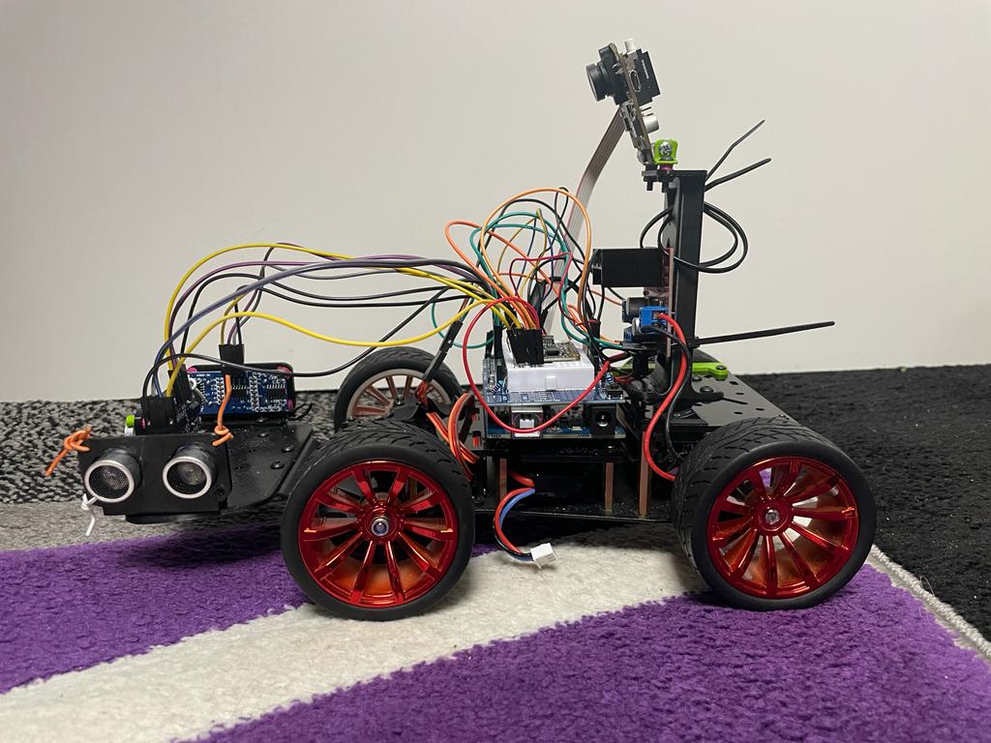
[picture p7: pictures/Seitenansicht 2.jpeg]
Seite1
  
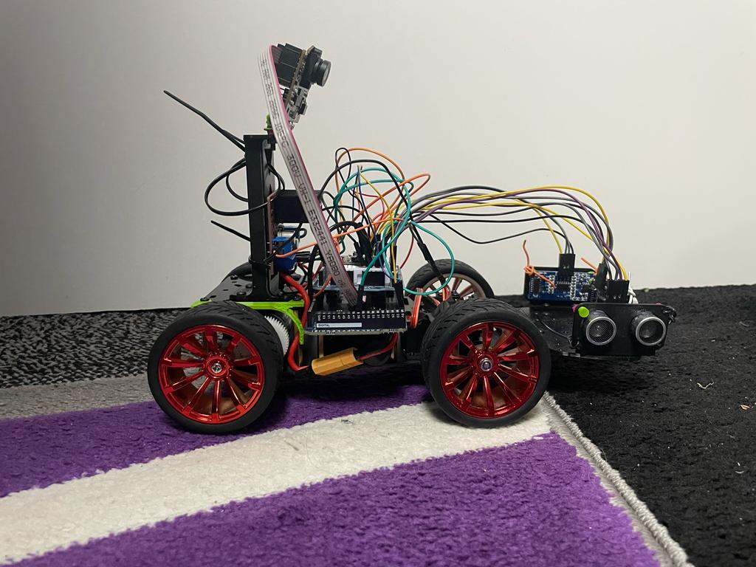
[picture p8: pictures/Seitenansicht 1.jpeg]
Seite2
  
</p>

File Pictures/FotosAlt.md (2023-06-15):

# Roboterfotos für die erste Runde in Chemnitz
Hier sind die Fotos des alten Roboters aus verschiedenen Ansichten zu sehen:
## Frontansicht

<p align="center">
  Front
</p>

## Hinteransicht

<p align="center">
  Hinten
</p>

## Oberansicht

<p align="center">
  Seite1
</p>

## Seitenansichten

<p align="center">
  Seite1
  Seite2
</p>

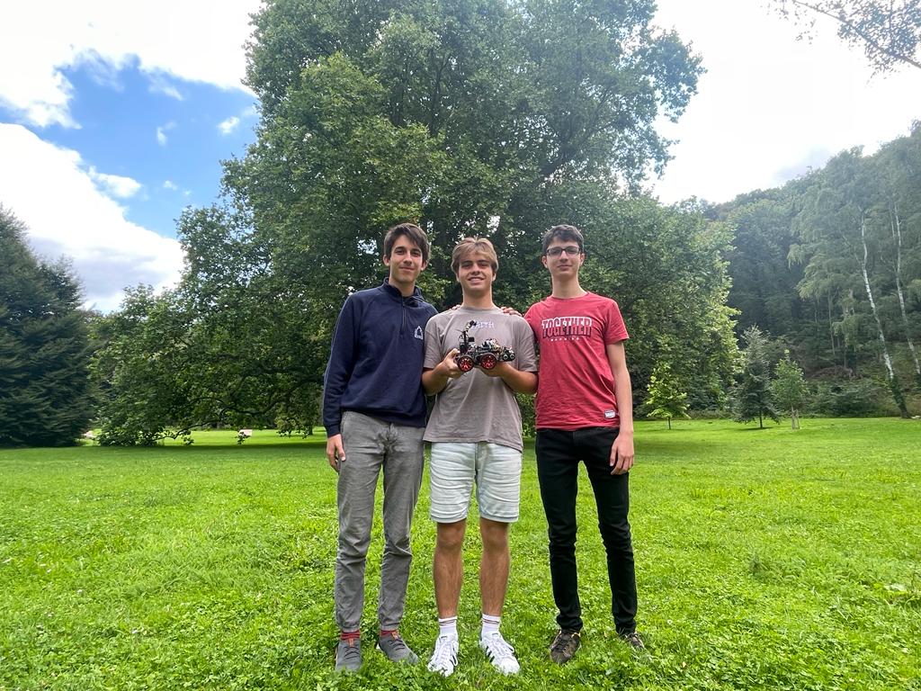
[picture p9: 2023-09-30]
pictures/team2.jpg

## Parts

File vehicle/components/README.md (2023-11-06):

# Components
Here we discuss the construction of the car and the 3D printed brackets

## Chassis
First, the planning of the chassis was started ([development](/development)). The current chassis consists of a large 3D-printed base plate to which the steering, the motor with the gearbox, the axles and the rest of the hardware are attached. The main requirements for the base plate are to shorten it compared to the previous base plate (Δl= -5cm) and to provide enough mounting options for the rest of the hardware. This resulted in the following design (only half of it can be seen because it was then later mirrored so that a complete plate is created).

Bildschirmfoto 2023-05-31 um 15 49 12

After printing out the part and screwing together the first components, it looks like this



The cover plate is placed on this base plate, on which the Arduino, the camera tower the driver and the battery are located. Particular attention should be paid to the holes in the middle, which facilitate cable management:



## Sensor base plate
The ultrasonic sensors should be mounted as far forward as possible on the robot in order to be able to react as early as possible to the coming obstacles or path changes. In order to mount this accordingly, a sensor base plate was designed that meets the requirements:

<p align="center">
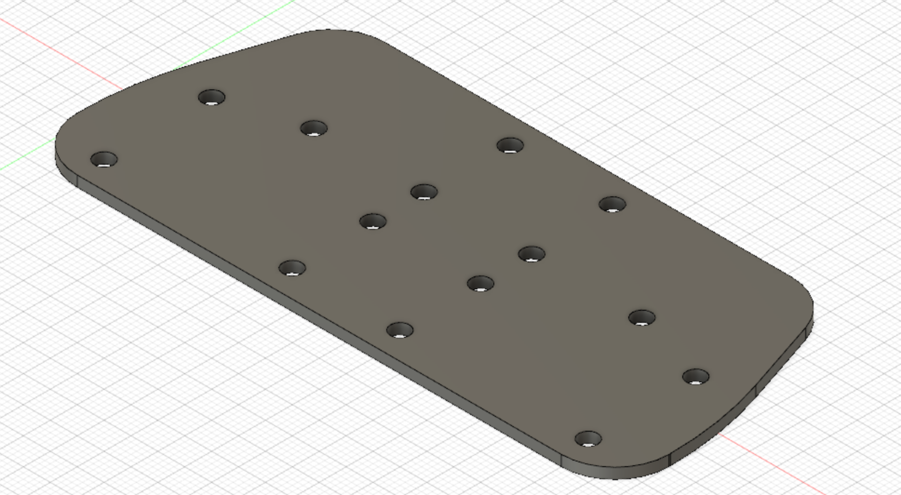
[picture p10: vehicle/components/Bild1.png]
sensor base plate
  
</p>

The holes are arranged to provide three sensor mounts with two holes each, four holes for the camera tower, and four for mounting to the chassis. 
Below is another picture of the component on the robot:

<p align="center">
  P2
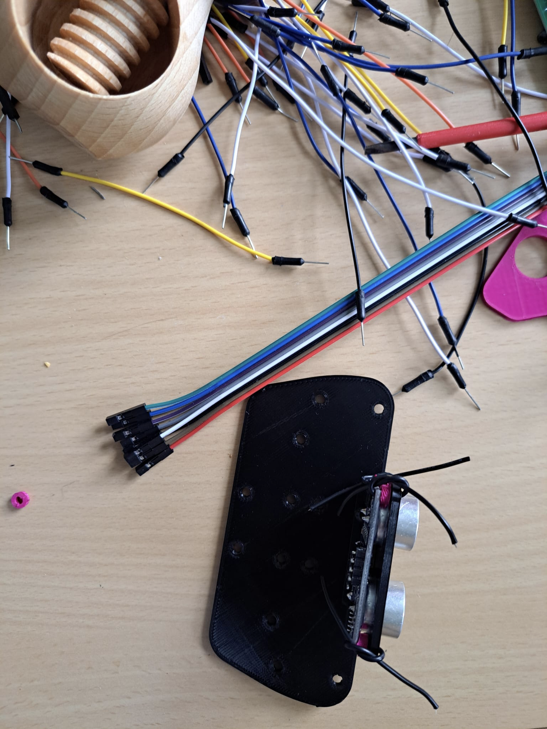
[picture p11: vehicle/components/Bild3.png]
P3
  
</p>

The camera tower was later built even further back on the car ([development](/development)).

# Ultrasonic sensor mount
The sensor mounting had to mount the ultrasonic sensors statically and opposite or perpendicular to each other in order to obtain trustworthy, reproducibly significant measured values. Therefore, the accuracy of the mounting is critical. Two large holes are used to hold the ultrasonic sensor transmitter and receiver, and the four holes around them are used to attach the sensor to the mount.

<p align="center">
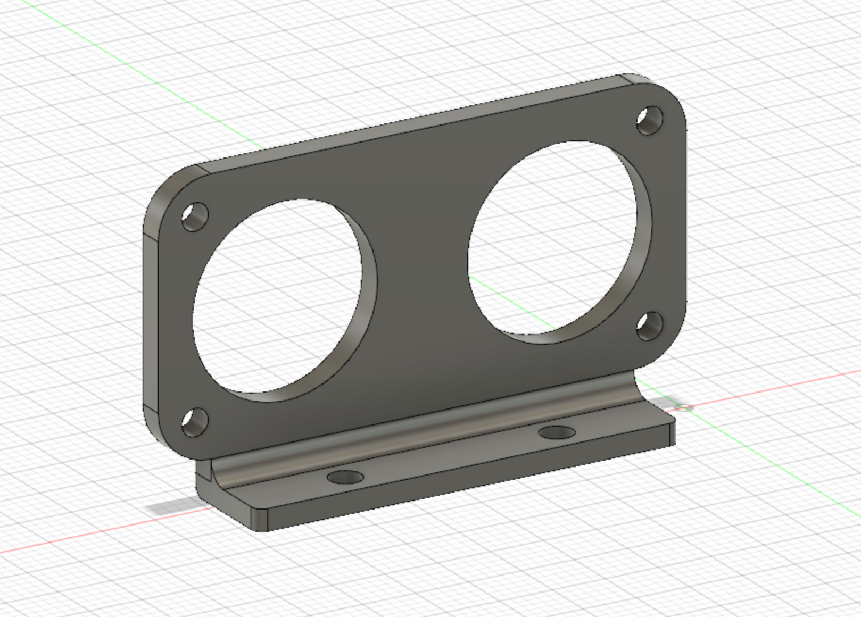
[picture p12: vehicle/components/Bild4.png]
P4
  
</p>

Small pins or wires are pushed through these, which can be melted or bent over on the other side. Between the holder and the sensor, the spacers are installed in such a way that the connection is as tight as possible, so that there is no lash and the sensors don't wobble unnecessarily. The holder is screwed to the base plate via the two holes on the bottom side (see sensor base plate).
  
<p align="center">
  P5
  P6
</p>

## Spacer
The spacers are needed to isolate or prevent grounding of different contacts and to limit distances between different components to one length. The template that was printed contains spacers with a height of 2.5mm and 5.0 mm to create different distances. The inner radius is 3.5mm so that the screws, which were mainly used, fit exactly so that there is resistance but you can screw the screws through. So the spacers can also be used as nuts.

<p align="center">
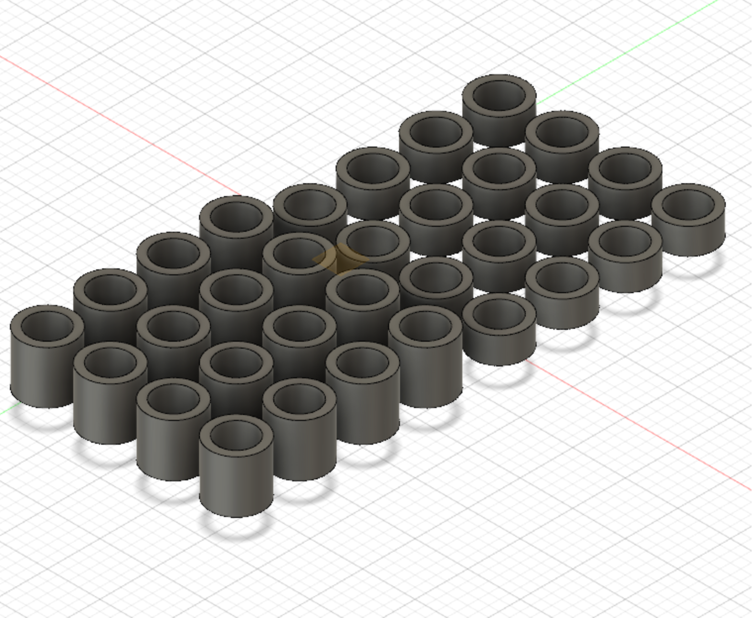
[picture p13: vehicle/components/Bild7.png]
P7
  
</p>
<p align="center">
  P8
  P9
</p>

## Fixing pins

The fixing pins consist of small plastic rods and a head. The rods are pushed through the mounting holes until the head is in contact with the mounting.
Then you can heat the other end briefly and then bend it over. This gives you a static, precise solution for attaching the sensors to the mounts. For test drives, however, cables were still used instead of the pins because they don't break as quickly. The disadvantage of cables or wires is that you can't attach them as tightly, which is why there is more slack.

<p align="center">
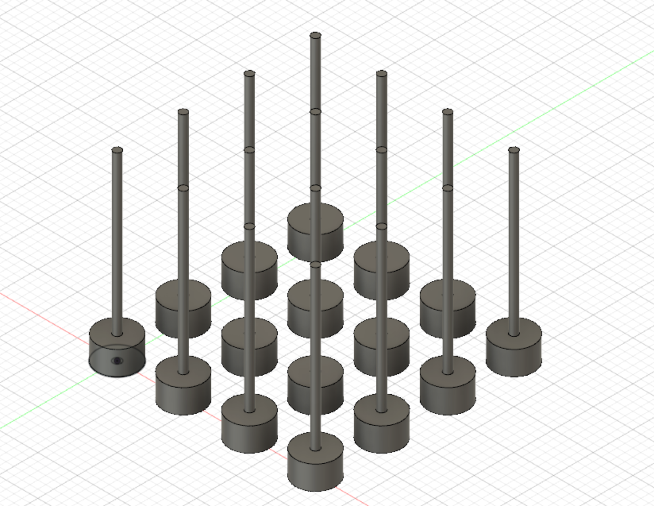
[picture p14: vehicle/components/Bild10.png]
P10
  
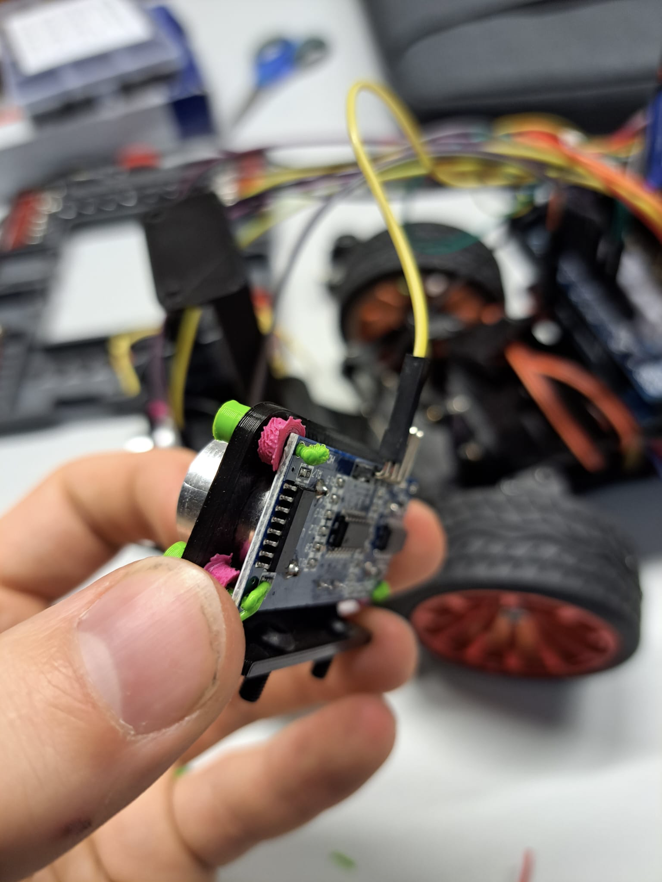
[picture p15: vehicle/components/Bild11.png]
P11
  
</p>

## Camera tower

The camera should be located as high as possible on the car (see [Camera Mounting Future Engineers Docs](https://github.com/World-Robot-Olympiad-Association/future-engineers-gs/blob/main/docs/p04-cv.md)), furthermore as far back as possible to ensure a large overview, to be able to detect obstacles as long as possible and to distinguish obstacles behind each other in terms of proximity. Therefore a camera tower was developed, on which later the camera with the camera angle holders is screwed:

<p align="center">
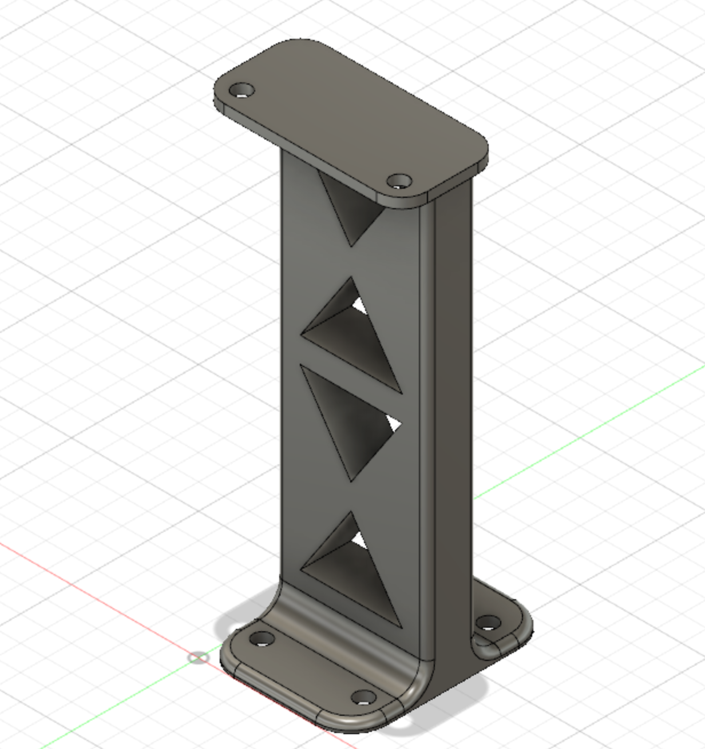
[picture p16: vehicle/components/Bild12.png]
P12
  
  P13
</p>

The triangles in the tower were inserted to save material and possibly roughly attach any components in the future.

## Camera angle holders

The angle holder attaches the mount of the camera to the camera tower. This was needed because the angles supplied with the camera had a thread and were therefore not compatible with our screws. But since the camera is supposed to be tiltable, which is not possible with the supplied setup, the printed angle holders helps to put the camera on a pedestal with the spacers and make them rotatable.

<p align="center">
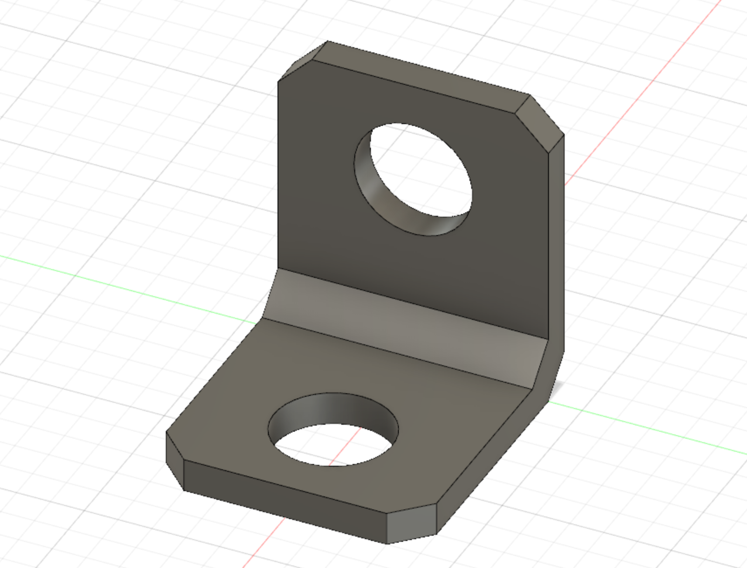
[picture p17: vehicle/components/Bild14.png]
P14
  
  P15
</p>

## Gear protection

The gear protection is a component that prevents any cables from getting near the gears:

<p align="center">
  P16
  P17
</p>

## Gearbox
Converting the conversion from large small to small large
<p align="center">
  Gearbox
</p>

## Battery holder

The most elegant solution seemed to be to attach the battery to the back of the car. For this purpose, we designed a battery box in which the battery can be placed. It consists of two parts (see 3D models), the A and B part, which are printed as individual parts and then glued. This gives a more accurate print because it eliminated the need for pressure supports. Below are pictures of the individual designs and the finished part:

Bildschirmfoto 2023-06-15 um 20 21 15
Bildschirmfoto 2023-06-15 um 20 21 27



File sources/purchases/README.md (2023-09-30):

## purchases

Stepping motor:  https://www.amazon.de/-/en/gp/aw/d/B08M8R35MQ?psc=1&ref=ppx_pop_mob_b_asin_image

Mega-R3 Microcontroller: https://www.amazon.de/-/en/gp/aw/d/B071D4KP6B?psc=1&ref=ppx_pop_mob_b_asin_image

Screw set: https://www.amazon.de/-/en/gp/aw/d/B09T7358Z9?psc=1&ref=ppx_pop_mob_b_asin_image

Multimeter:    https://www.amazon.de/-/en/gp/aw/d/B07H824437?psc=1&ref=ppx_pop_mob_b_asin_image

Battery set:  https://www.amazon.de/-/en/gp/aw/d/B09K4ZBPBF?psc=1&ref=ppx_pop_mob_b_asin_image

Adapter cable:  https://www.berrybase.de/sparkfun-qwiic-adapterkabel-4-pin-dupont-male-150mm

Gyro sensor:   https://www.berrybase.de/adafruit-9-dof-orientation-imu-fusion-breakout-bno085-bno080

Funduino-set:  https://funduinoshop.com/projekte/mikroelektronik/projektsets/world-robot-olympiad-future-engineers-set-2023

Expansion-Board:  https://www.amazon.de/Hailege-Prototype-Expansion-Breadboard-ProtoShield/dp/B0BN1M2SNG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

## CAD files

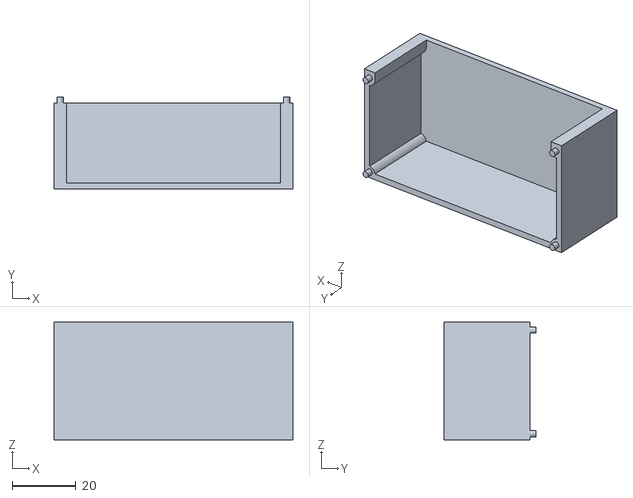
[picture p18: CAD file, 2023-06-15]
vehicle/3Dprinting/Batterie_Halterung_TeilB.stl
75.0 x 29.0 x 37.0

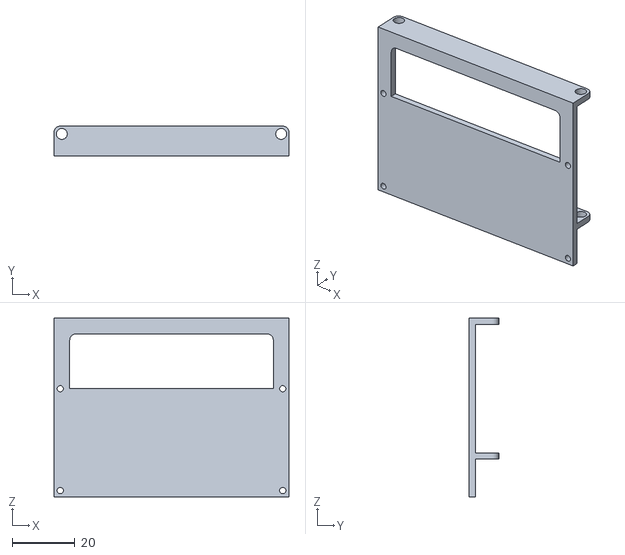
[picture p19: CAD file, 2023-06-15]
vehicle/3Dprinting/Batterie_Halterung_TeilA.stl
75.0 x 9.50 x 57.0

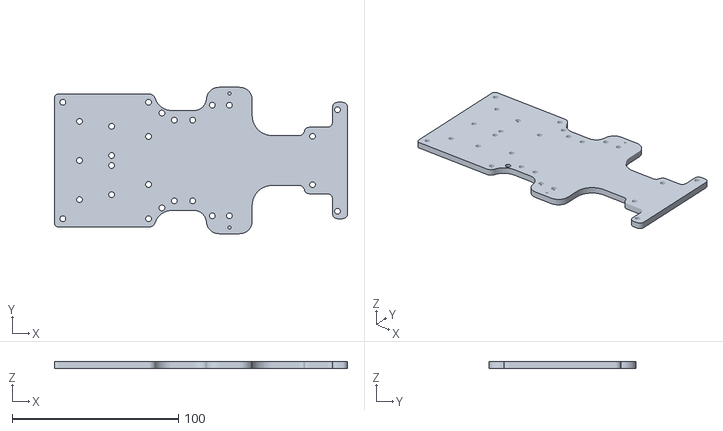
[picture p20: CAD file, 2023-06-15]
vehicle/3Dprinting/Auto_Chassis_Grundplatte.stl
176.0 x 88.0 x 4.00

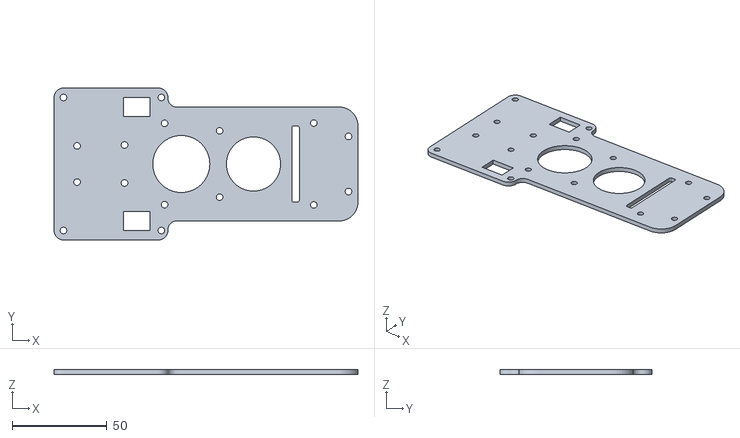
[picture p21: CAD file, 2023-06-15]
vehicle/3Dprinting/Auto_Chassis_Deckplatte.stl
160.0 x 80.0 x 2.50

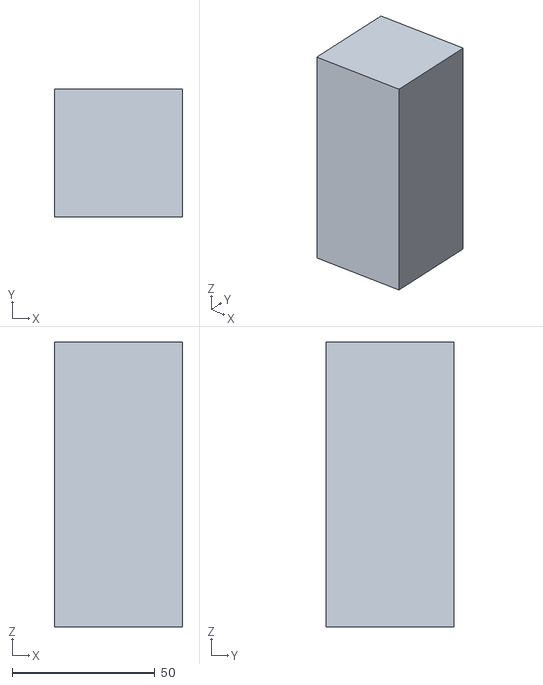
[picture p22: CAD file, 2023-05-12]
vehicle/3Dprinting/Obstacle.stl
45.0 x 45.0 x 100.0

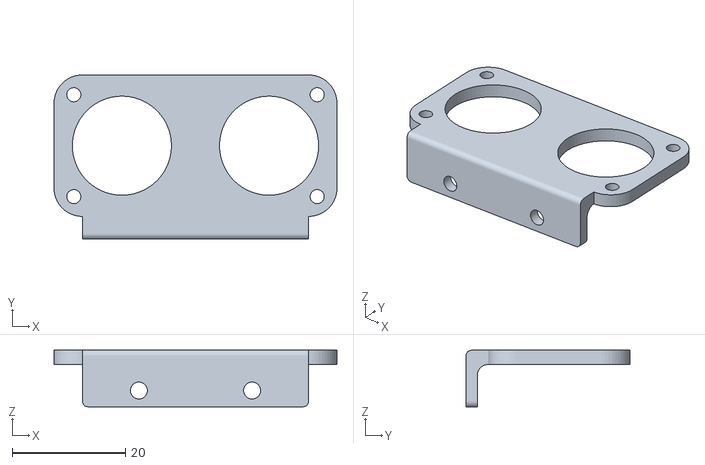
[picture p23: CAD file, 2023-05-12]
vehicle/3Dprinting/Ultraschallsensor_Halterung.stl
50.0 x 29.0 x 10.0

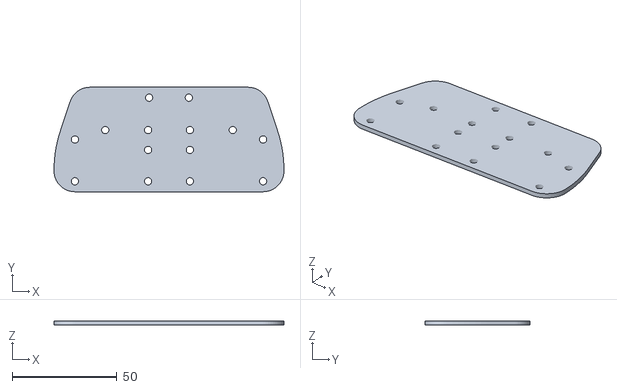
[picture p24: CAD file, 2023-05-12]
vehicle/3Dprinting/Sensoren_Grundplatte.stl
110.0 x 50.0 x 2.00

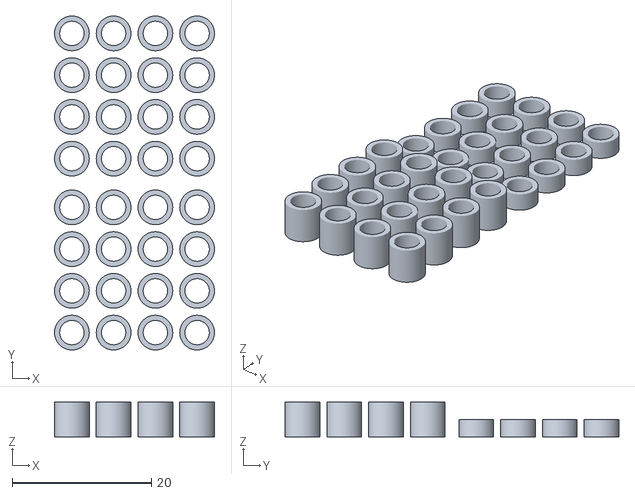
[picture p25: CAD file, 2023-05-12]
vehicle/3Dprinting/Placeholder_Template.stl
23.0 x 48.0 x 5.00

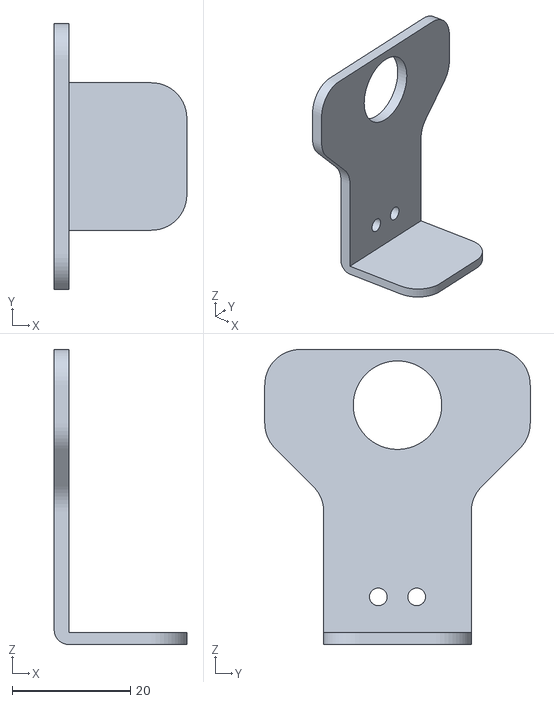
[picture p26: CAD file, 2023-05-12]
vehicle/3Dprinting/Kamera_Winkelhalter_Mark1.stl
22.5 x 45.0 x 50.0

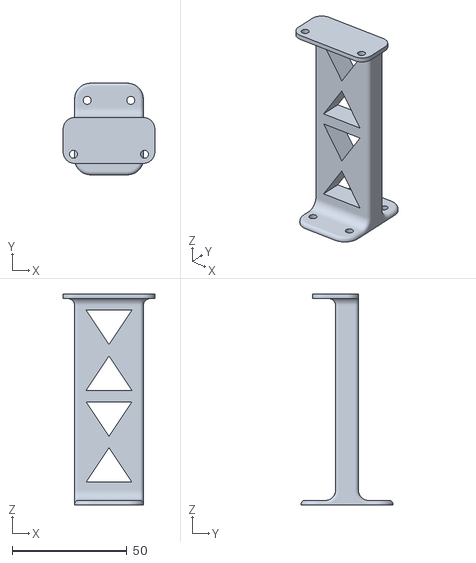
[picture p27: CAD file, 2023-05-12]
vehicle/3Dprinting/Kamera_Ständer.stl
40.0 x 40.0 x 92.0

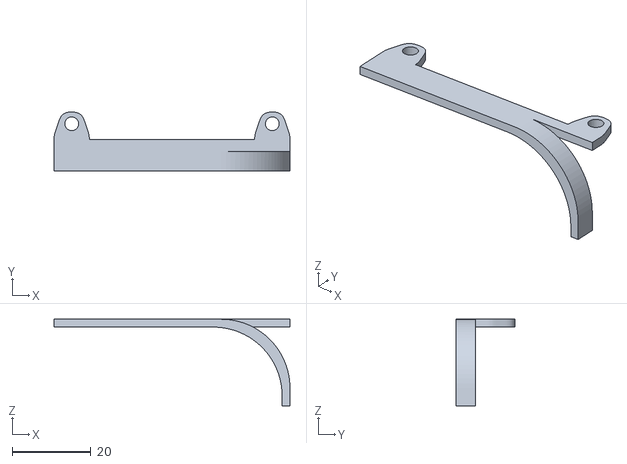
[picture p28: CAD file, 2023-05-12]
vehicle/3Dprinting/Zahnradschutz.stl
60.0 x 15.0 x 22.0

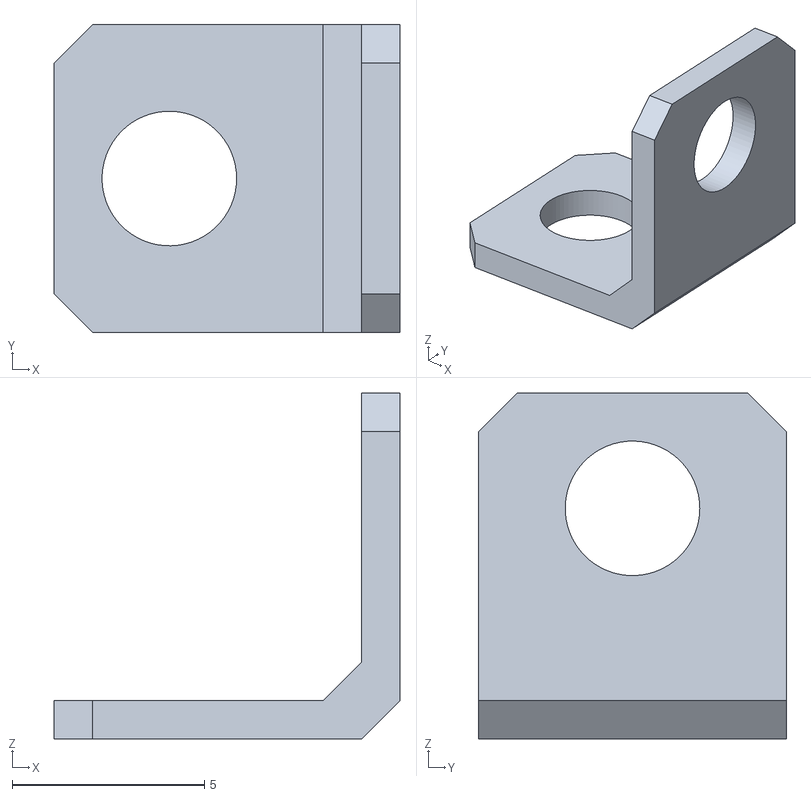
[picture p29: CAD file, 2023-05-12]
vehicle/3Dprinting/Winkelhalter.stl
9.00 x 8.00 x 9.00

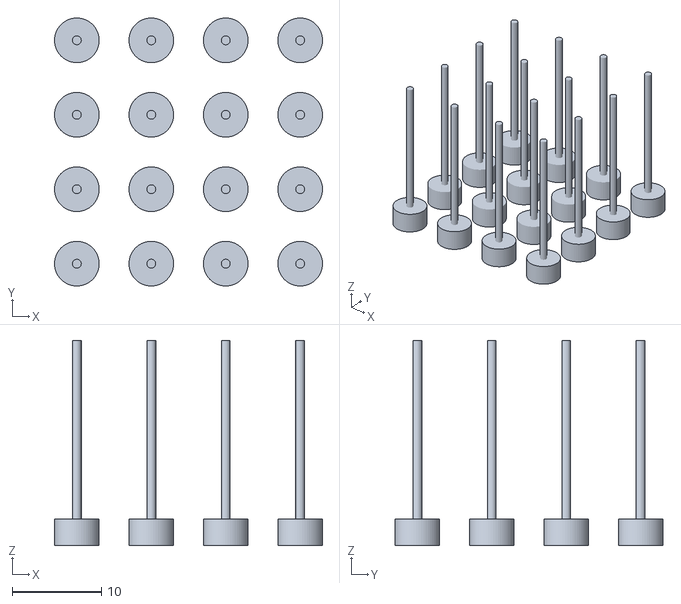
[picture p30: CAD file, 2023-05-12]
vehicle/3Dprinting/Halterungspins_Template.stl
30.0 x 30.0 x 23.0

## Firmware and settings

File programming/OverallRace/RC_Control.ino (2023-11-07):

#include "variables.h"  // all the vars, actuators, and sensors are defined and initialized here.
#include "ControlRC.h"  // all functions for control, read sonsor and update variables are located here


void setup() {
  Serial.begin(9600);
  while (!Serial) delay(10);
  initializeHardware();
  drivingDC.setForward();
}


int numRounds = 3;
int Stoptime = 6;
unsigned long tim = 0;
void loop() {
  updateControlData();
  drivingDC.drive(velocity);
  control_servo();
  //print();  //zzzzzzz

  if (redturn == 2 && turns == 8 && Sumcheck && redcheck) { // color = 2, end of round 2 and redcheck = true
    tim = millis() + 1000;  // drive for a second in such a way you will become straight
    while (tim > millis()) {
      drivingDC.drive(velocity);
      steeringServo.drive(-1 * roll);
    }

    //moving direction is backwards
    drivingDC.drive(0);
    drivingDC.setBackward();

    // drive until you are out of the straight section
    while (distances[1] + distances[2] < 150 || distances[0] < 150) {
      drivingDC.drive(velocity);
      steeringServo.drive(0);
    }

    //drive for one more second backwards
    tim = millis() + 1000;
    while (tim > millis()) {
      drivingDC.drive(velocity);
      steeringServo.drive(0);
    }

    // change the moving direction
    drivingDC.drive(0);
    drivingDC.setForward();
    referenceAngle = referenceAngle + 90 * direction; // For the car now appears so as if a curve is on his left which is why he will turn to the left.
    theoreticalAngle = theoreticalAngle + 90 * direction;

    // let him drive till he is in the straight section
    while (distances[1] + distances[2] > 150 || distances[0] > 150) {
      updateControlData();
      drivingDC.drive(velocity);
      control_servo();
    }

    direction = direction * (-1);     // changing the sign of direction so he turns right
    redcheck = false; // to ensure he will never get in here again.
  }

  if (turns == 4 * numRounds) {
    tim = millis() + Stoptime * 1000;
    while (distances[0] > 120 || !Sumcheck || tim > millis()) {  // drive for at least tim and until frontDistance is less than 120 and SumDistance is less than 100
      updateControlData();
      drivingDC.drive(velocity);
      control_servo();
    }
    while (1) {
      control_servo();
      drivingDC.drive(0);
      delay(100);
    }
  }
}



void print() {
  float k = (distances[0] - (67578.1 / (cam.get_Blocksize() + 514.89) - 13.4431) - 80) * (0.5 * direction * (abs(cam.get_color() - 1) - min(1, 2 - cam.get_color())) + max(0.5, 1 - 0.5 * cam.get_color()));
  Serial.print("referenceAngle ");
  Serial.print(referenceAngle);
  Serial.print("       targetAngle ");
  Serial.print(controlDataArr[0]);
  Serial.print("       roll ");
  Serial.print(roll);
  Serial.print("       rightShift ");
  Serial.print(rightShift);
  Serial.print("       camShift ");
  Serial.print(camShift);
  Serial.print("       cam steerin ");
  Serial.print(hh);
  Serial.print("       wallShift ");
  Serial.print(wallShift);
  Serial.print("       frontdistance ");
  Serial.print(distances[0]);
  Serial.print("       rightdistance ");
  Serial.print(distances[1]);
  Serial.print("       leftdistance ");
  Serial.print(distances[2]);
  Serial.print("       sumdistance ");
  Serial.print(distances[2] + distances[1]);
  Serial.print("       sumcheck ");
  Serial.print(Sumcheck);
  Serial.print("       size ");
  Serial.print(cam.get_Blocksize());
  Serial.print("       Blockdistance ");
  Serial.print(k);
  Serial.print("       function ");
  Serial.print(k < 0 && k > -35 ? 0 : 1);
  Serial.print("        x_pos  ");
  Serial.print(cam.get_x_pos());
  Serial.print("        frameWidth  ");
  Serial.print(cam.get_frameWidth());
  Serial.print("        correction ");
  Serial.print(1 - 1 / cam.get_frameWidth() * abs(cam.get_x_pos()));
  Serial.print("       color ");
  Serial.println(cam.get_color());
}

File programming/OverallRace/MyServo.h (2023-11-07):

#ifndef MyServo_h
#define MyServo_h

#include <Arduino.h>
#include <Servo.h>
class MyServo {
private:
  byte pin;
  byte servo_PWMpin;
  byte limitR = 133;  //angle must be< 120
  byte limitL = 20;   //angle must be >35
  byte straightAngle = 90;
  Servo steeringServo;

public:
  MyServo() {}  //Default constructor  // do not use

  MyServo(byte pin, byte servo_PWMpin) {
    this->pin = pin;
  }

  void init() {
    steeringServo.attach(pin);
    pinMode(pin, OUTPUT);
    int PWMSignal = 255;  //can vary betwwen 0 and 255
    analogWrite(servo_PWMpin, PWMSignal);
    reset();
  }

  void reset() {
    steeringServo.write(straightAngle);
  }

  // value =0 ==> straightAngle / value =1 ==> limitR / value =-1 ==> limitL
  double drive(float value) {
    value = min(1, max(-1, value));
    int sgn = (value == 0 ? 0 : 0.5 * value / abs(value) - 0.5);
    value = (limitR * (sgn + 1) + limitL * sgn - straightAngle * 2 * (sgn + 0.5)) * value + straightAngle;
    steeringServo.write(value);
    return value;
  }
};


#endif

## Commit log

2023-05-10 Create Sensoren
2023-06-15 Create Motorik
2023-06-15 Create README.md
    Hier ist die Motorik unseres Roboters enthalten
2023-09-30 new name
    [Auto_Chassis_Deckplatte.stl, Auto_Chassis_Grundplatte.stl, Batterie_Halterung_TeilA.stl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]
2023-09-30 new folder
    [FE.fzz]
2023-09-30 new structure
    [Auto_Chassis_Deckplatte.stl]
2023-11-07 Update README.md
    Motors
